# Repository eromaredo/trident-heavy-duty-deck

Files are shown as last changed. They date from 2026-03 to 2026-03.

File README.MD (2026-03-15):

# Heavy Duty Deck Panel for Voron Trident (Preview)

> [!CAUTION]
> I put a lot of effort into keeping all dimensions correct, but I haven't tested it in real life **yet** — only against Voron's official STEP file for a 250mm build and my own 350mm 4040 build. Please check the dimensions before ordering.

## Overview

This repository contains a parametric aluminium deck panel cover for the Voron Trident, made by someone who is not a CAD designer — so I apologize in advance for anything you may find in the `.f3d` file. I have seen a few similar projects with solid mounts for Z motors, but none of them appealed to me. This design makes no compromises: just one big, sturdy piece of aluminium.

All `.dxf` files were generated using the default values from the table below. If you need to change them, open the file in Autodesk Fusion, adjust the parameters or edit the `BaseDrawing` sketch.

## Features

- One mounting plate for the Z motors ensures all of them are level and aligned.
- Seals the bottom of the chamber, reducing hot air leakage.
- Two holes near the rear center for PG cable glands, separating high voltage and data cables — left (PG7) for 230V bed power, right (PG11) for thermistors, bed fans, CAN cables, etc.
- Two PG9 holes on the rear corners. These will fit sixteen AWG24 cables — enough for one side of an AWD setup, thermistors, and possibly fans. See [images](/image/) for visualisation.

## BOM

Assuming deck thickes of 4 mm and utilising DXFs from the repository.

| Part Name | 250 mm | 300 mm | 350 mm |
| --- | --- | --- | --- |
| M5x8 BHCS | 21 | 24 | 27 |
| M5 Roll in Spring T-Nut | 21 | 24 | 27 |
| PG 7 Cable Gland | 1 | 1 | 1 |
| PG 9 Cable Gland | 2 | 2 | 2 |
| PG 11 Cable Gland | 1 | 1 | 1 |

## Customisng the design

### Public Parameters

| Name | Description | Default Value |
| ---- | --- | --- |
| corner_brackets_z_length | Extends cut-outs on left and right sides of Z vertical extrusion to accommodate 90° corner brackets | `0 mm` |
| cut_tolerance | How much the external perimeter should be sized down to fit CNC machine tolerance | `0.15 mm` |
| extrusion_horizontal_length | Length of a horizontal side extrusion. `120 mm` for `0 mm` bed size. Every additional `mm` will reflect bed size. For `250 mm` bed size it'll be `120 mm + 250 mm = 370 mm`. | `120 mm + 250 mm` |
| screw_m3_diam | M3 screw hole dimension (must include cut tolerance) | `3.5 mm` |
| screw_m5_diam | M5 screw hole dimension (must include cut tolerance) | `5.5 mm` |
| screw_m5_number_long | How many M5 screw holes should be added on the left, front and right edges. Recommended `5` for `370 mm` `extrusion_horizontal_length` and one for every additional `50 mm`. | `5`/`6`/`7` |
| screw_m5_number_short | How many M5 screw holes should be added on both back edges (left and right). | `3` |

All parameters with an `_` prefix are internal and I don't recommend changing them. I left a few internal variables with different PG Cable Glands sizes which can be used in case of someone would like to modify some hole sizes. All values include small offset.

- `_pgX_drill_hole` - Hole for mounting PG Cable Gland with 0.5 mm offset
- `_pgX_outrer_diam` - Width of the bottom nut with small offset to distance it from extrusion

| Name | Value |
| --- | --- |
| _pg7_drill_hole | 13 mm |
| _pg7_outer_diam | 25 mm |
| _pg9_drill_hole | 15.5 mm |
| _pg9_outer_diam | 29 mm |
| _pg11_drill_hole | 19 mm |
| _pg11_outer_diam | 32 mm |
| _pg13_5_drill_hole | 21 mm |
| _pg13_5_outer_diam | 36 mm |

## Footnotes

[Kradex PG cable glands](https://www.kradex.com.pl/product/accessories/d%c5%82awnica?lang=en) were used in this project, so please compare the dimensions. [Here is  direct link](https://www.kradex.com.pl/products/1102/D%C5%82awnica_Dimension_table.pdf) to the dimension table.

The files are distributed under Apache 2.0 licence.

In case of any issues or ideas, open an issue ticket please.

## Render

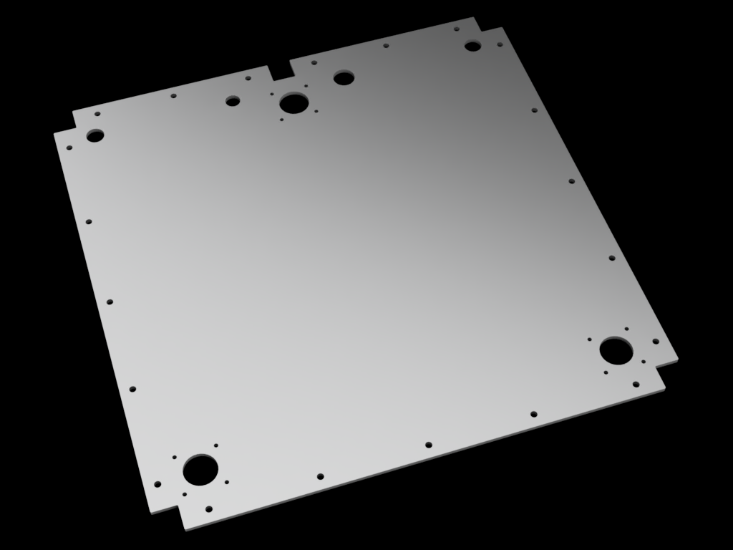
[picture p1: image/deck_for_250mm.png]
Render of the deck panel for 250 mm bed size


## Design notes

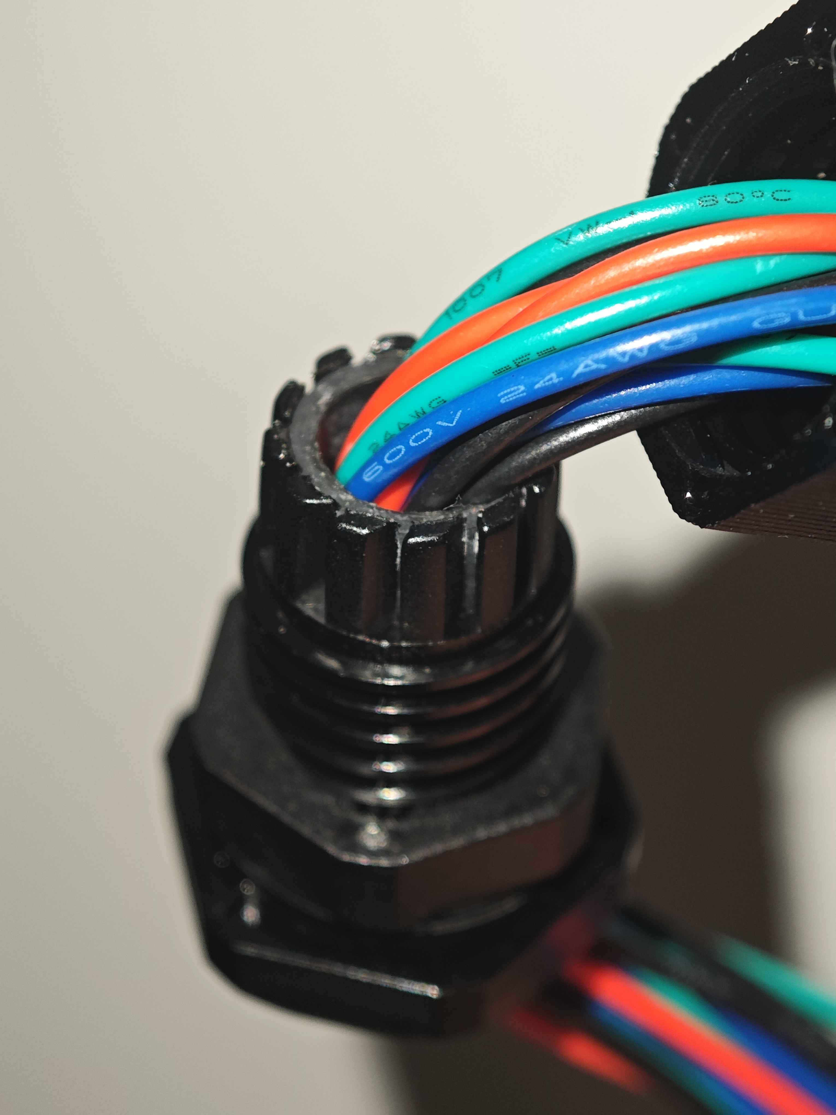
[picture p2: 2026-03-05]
image/pg9_1.jpg

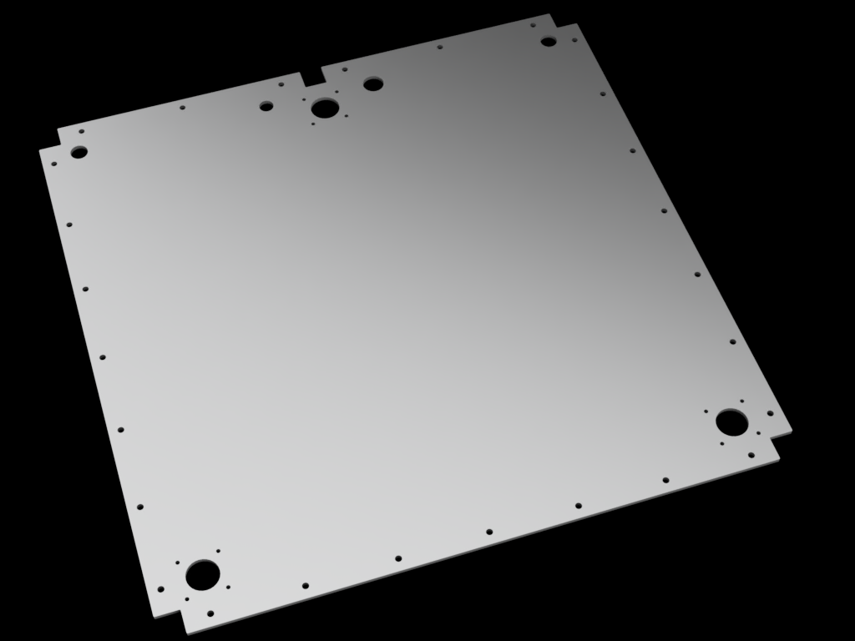
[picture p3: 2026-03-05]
image/deck_for_350mm.png

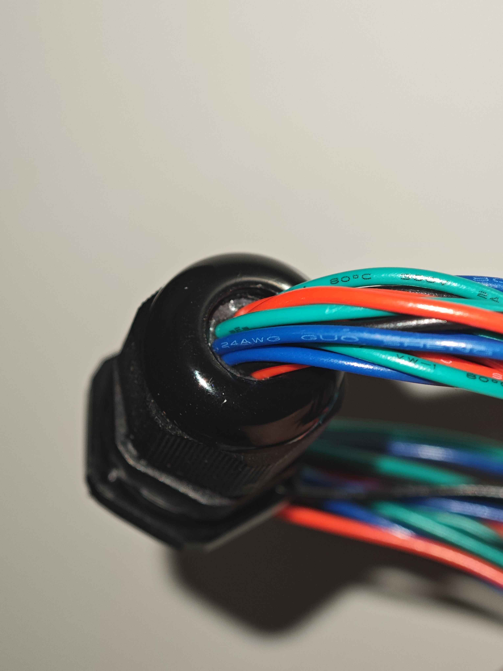
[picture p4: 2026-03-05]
image/pg9_2.jpg

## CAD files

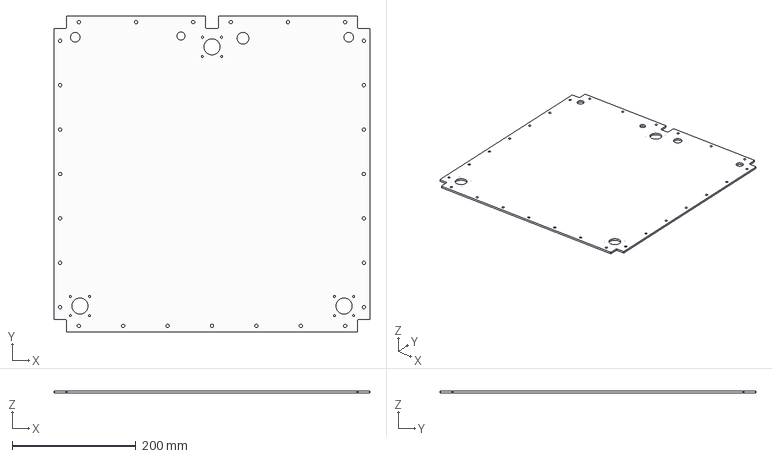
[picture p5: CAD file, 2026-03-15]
CAD/Trident-Heavy-Duty-Deck.step
509.7 x 509.7 x 4.00 mm

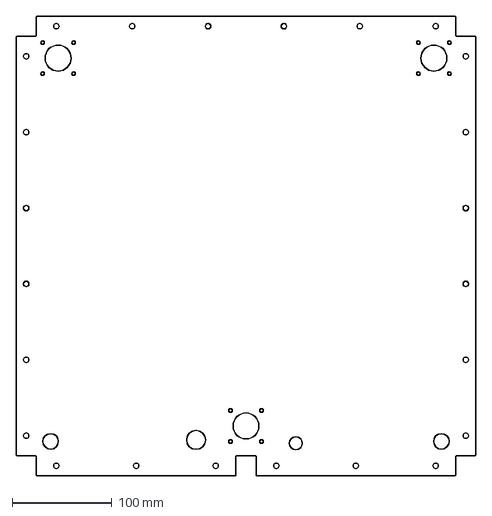
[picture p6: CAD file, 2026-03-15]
Drawings_DXFs/Trident-Heavy-Duty-Deck-300mm.dxf
459.7 x 459.7 mm

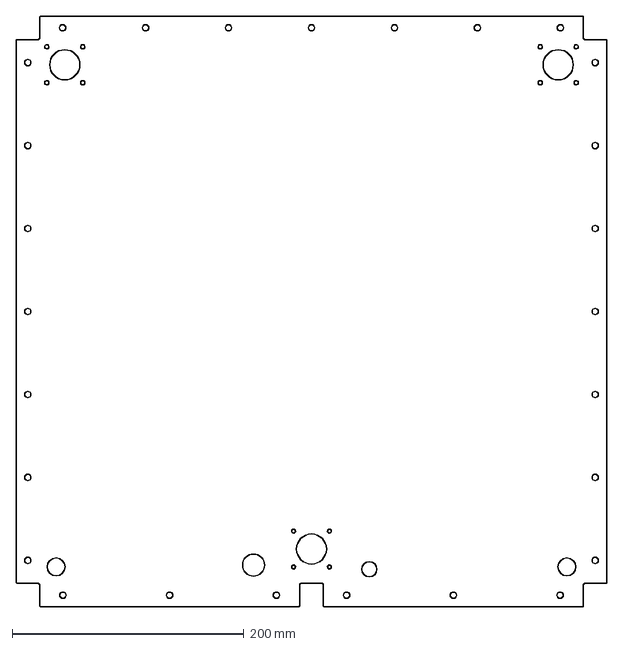
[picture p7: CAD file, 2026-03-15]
Drawings_DXFs/Trident-Heavy-Duty-Deck-350mm.dxf
509.7 x 509.7 mm

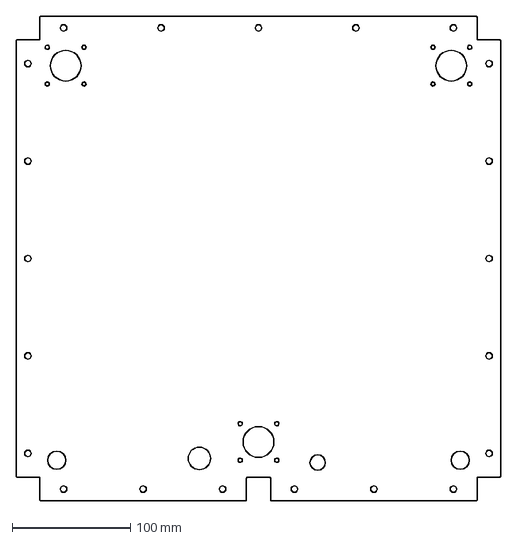
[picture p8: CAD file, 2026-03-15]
Drawings_DXFs/Trident-Heavy-Duty-Deck-250mm.dxf
409.7 x 409.7 mm

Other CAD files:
CAD/Trident-Heavy-Duty-Deck.f3d

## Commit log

2026-02-27 First iteration
    [Trident-Heavy-Duty-Deck-250mm.dxf, Trident-Heavy-Duty-Deck-300mm.dxf, Trident-Heavy-Duty-Deck-350mm.dxf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]
2026-03-05 Added PG Glands Removed m3 hole for cable strain as it might not be needed Readme.md update
    [Trident-Heavy-Duty-Deck-250mm.dxf, Trident-Heavy-Duty-Deck-300mm.dxf, Trident-Heavy-Duty-Deck-350mm.dxf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]
2026-03-05 Added two additional holes for motors and thermistors cables Changes PG13.5 to PG11 as motor cables are now routed separately
    [Trident-Heavy-Duty-Deck-250mm.dxf, Trident-Heavy-Duty-Deck-300mm.dxf, Trident-Heavy-Duty-Deck-350mm.dxf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]
2026-03-05 Fixed incorrect PG11 hole position
    [Trident-Heavy-Duty-Deck-250mm.dxf, Trident-Heavy-Duty-Deck-300mm.dxf, Trident-Heavy-Duty-Deck-350mm.dxf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]
2026-03-05 Changed corners PG7 with PG9 to fit AWD
    [Trident-Heavy-Duty-Deck-250mm.dxf, Trident-Heavy-Duty-Deck-300mm.dxf, Trident-Heavy-Duty-Deck-350mm.dxf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]
2026-03-14 Increased offsets for pgs Fixed issue where cut tolerance for Z extrusion was added twice
    [Trident-Heavy-Duty-Deck-250mm.dxf, Trident-Heavy-Duty-Deck-300mm.dxf, Trident-Heavy-Duty-Deck-350mm.dxf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]
2026-03-15 Updated STEP file
    [Trident-Heavy-Duty-Deck.step]
